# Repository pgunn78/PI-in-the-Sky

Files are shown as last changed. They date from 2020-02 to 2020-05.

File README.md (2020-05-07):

# PI-in-the-Sky
Our first semester project
## Planning
### Goals
Launch a raspberry pi into the sky measuring and recording accelerometer data along it's flight and ensure that the pi is not broken when it lands.
### Method
Using a air canon we will launch a inclosed capsule which will hold a Raspberry Pi which will be the brain of the missle, accelerometer to both measure its momentum and to know when to trigger its parachute, battery to power the Pi and Acclerometer, and parachute to slow its decent once its triggered. We can additionaly attempt to mount the air canon on somesort of mount so that it's easier to handel
### Materials
1. PVC tubing both 2 inch and 3 inch
2. Valve
3. air compressor
5. ABS plastic
6. wires
7. small lithium ion battery
8. accelerometer
9. Raspberry PI
10. 1 large parachute or multiple smaller parachutes
11. fittings
12. PVC glue/sealent
13. PVC glue Primer
14. Nuts and Bolts
15. 3mm plastic sheets
16. springs
17. PCB single sided copper material
### Timeline
#### weeks 1-2: planning and modeling
-finish projectile model
-decide on launch method
-start design of launch method
-source springs and materials
#### weeks 3-6: construction testing/Coding
-find out how to determine tilt
-build launch method
-assemble projectile
-milling of PCB
#### week 7-10: troubleshooting and polishing
-ensure that projectile stays level in flight
-work out kinks in parachute deployment
#### week 11: Launch
-launch projectile get data and assemble it into more easily understood graph
### Inital Design
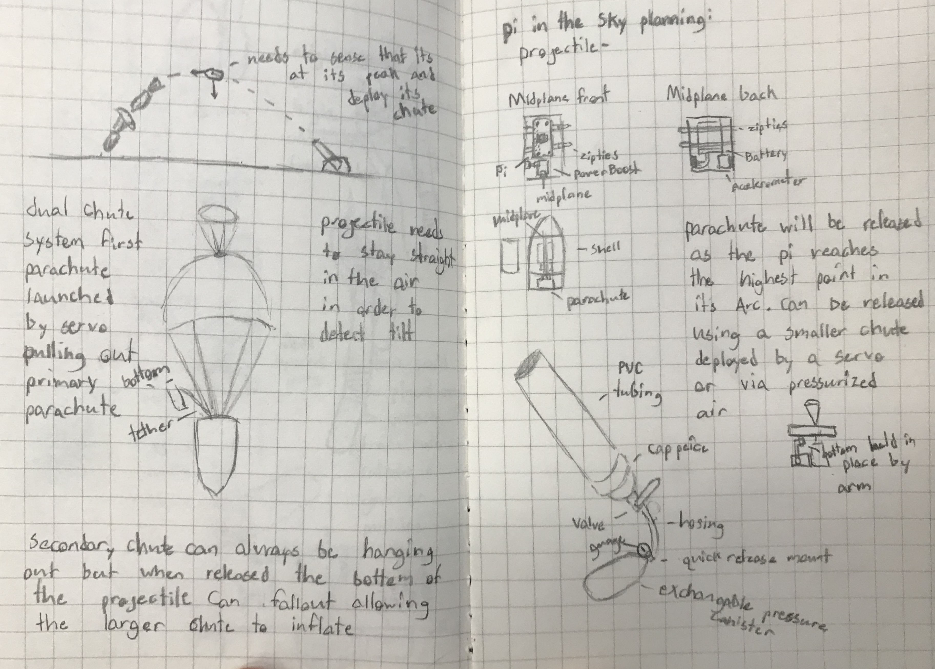
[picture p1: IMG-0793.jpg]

### Solidworks Design
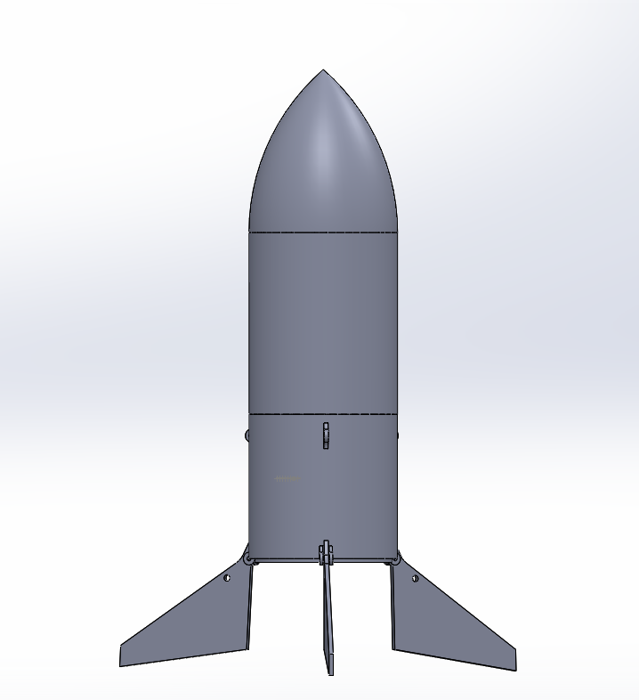
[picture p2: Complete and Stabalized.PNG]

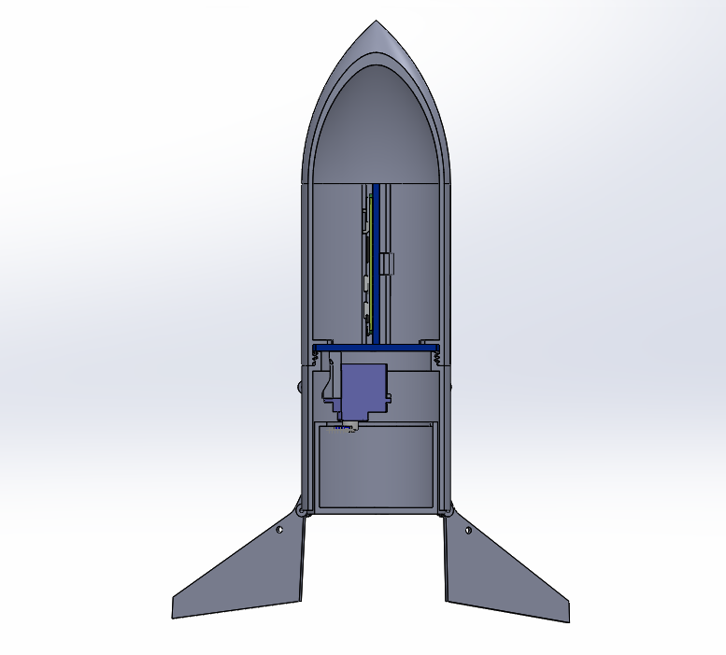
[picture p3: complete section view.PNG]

#### Design Overview
The components such as the Pi and battery are mounted on the midplane and held in place by a cap which has a hole cut in the center to run wires to a servo. Which opens to release the parachute hatch to slow down the projectile once the projectile reaches its maximum altitude. to maintain a level flight fins are mounted on the side with small extrusions to keep them held out at an ideal position.
### Code 

```

import Adafruit_LSM303
import Adafruit_GPIO.SPI as SPI
import time
import RPi.GPIO as GPIO
import pigpio
from time import sleep
#the Pi stuff below is how we get a smooth servo turn
#it just makes the pi send smother infromation waves
pi = pigpio.pi()
pi.set_mode(17, pigpio.OUTPUT)
pi.set_PWM_frequency(17,50)
sleep(1)
print(pi.get_PWM_frequency(17))

lsm303 = Adafruit_LSM303.LSM303()

while True:
    # Read the X, Y, Z axis acceleration values and print them. accel is the acceleration mag is the direction/angle
    accel, mag = lsm303.read()
    # Grab the X, Y, Z components from the reading and print them out.
    accel_x, accel_y, accel_z = accel
    mag_x, mag_y, mag_z = mag

    if 540 > mag_x > 510:
        pi.set_servo_pulsewidth(17,500)
        sleep(1)
        pi.set_servo_pulsewidth(17,2500)
        sleep(1)

    print('Mag X={0}, Mag Y={1}, Mag Z={2}'.format(
        mag_x, mag_y, mag_z))
    time.sleep(1)

```

### Wiring and PCB design
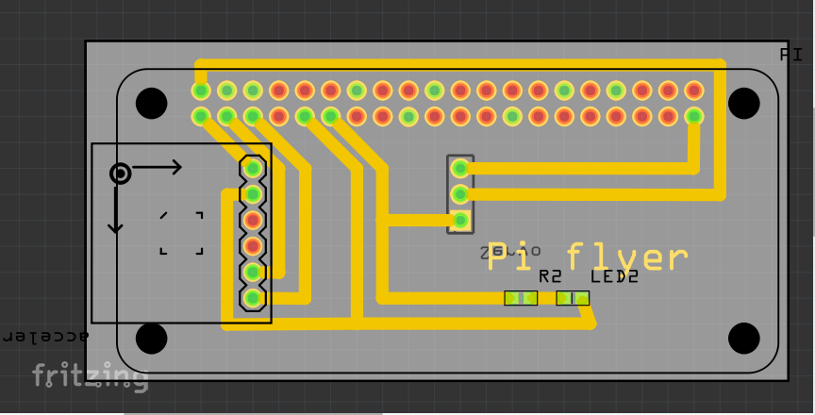
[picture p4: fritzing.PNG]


## Problems and Solutions
### SolidWorks
While doing the solidworks design the most major problem that we encountered was material use, sizeing of the projectile, and space efficiency. due to it's cylindrical shape the space inside was not the easiest to utalize properly and effectlivly while still securing the components so that they won't shift during flight. To fix this we added a midplane to secure the components onto and added another plane above that to fix the midplane during flight. In addition to providing a place to mount components this also provides ease of construction allowing us to fix all components before sliding the midplane into the projectile where there is much less space to work. by designing the projectile in a fairly bullet like shape we made it difficult for the projectile to be printed without a large amount of support material to minimize the support material needed we added a steeper slope to the shape and went into the advanced settings of the print job turning the angle down where support material was needed and allowing us to print the entire part without any material needed for the central point. The last major problem that we encountered was the sizing of certain features such as the threads which were done using the solidworks thread tool (Creating suprisingly good results). this could still present a problem as the ABC plastic is maluable enough to where a impact from the side can seperate the two pieces. Which might cause the parachute compartment to breakup when deployed spilling the internals out mid-flight, but it seems like a fairly strong connection along the length of the projectile.
### Construction of the Projectile
the largest problems in the construction of the Projectile was the header hight, PCB milling and sourcing of materials. When milling our PCB we broke the job into two different sections due to class time limitations, cutting the traces or the copper wire paths first, and then drilling the holes for the headers. this caused the holes and traces to become slightly misaligned although it did not significantly damage the board or prevent it from working. the Headers on the PCB also prevented the midplane from sliding in due to their hight to fix this we bent the header pins down in the process breaking one of the copper traces which was repaired using a section of wire which was striped of insulations and soldered on. in addition to this the LED on the board was connected to the signal pin of the servo which we fixed by breaking the connection and soldering a wire from 3V to the broken connection. The method of launching the parachute was initally a spring which with the help of a servo controlled latch would realease the parachute, both the sourcing of a spring that would meet the diminsions we needed and could store the required force was difficult prompting us to use a secondary parachute which would pull out the bottom utalizing the same servo release mechanism.

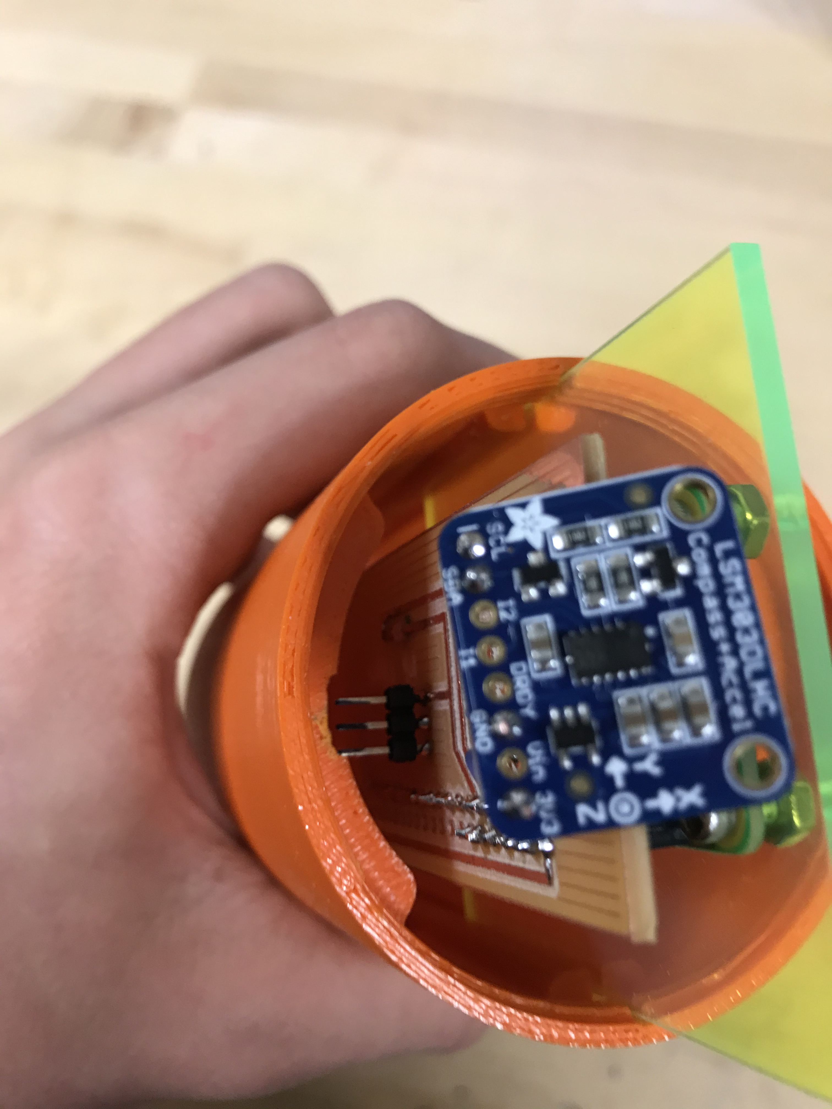
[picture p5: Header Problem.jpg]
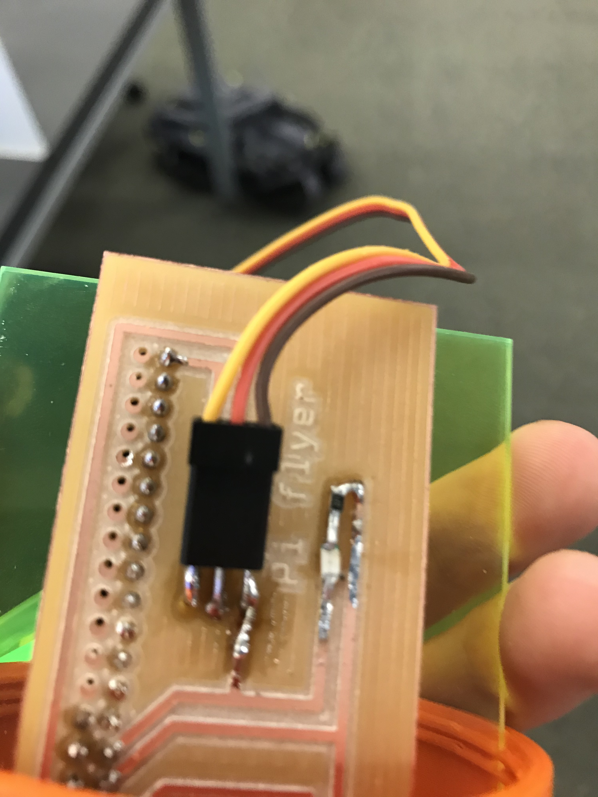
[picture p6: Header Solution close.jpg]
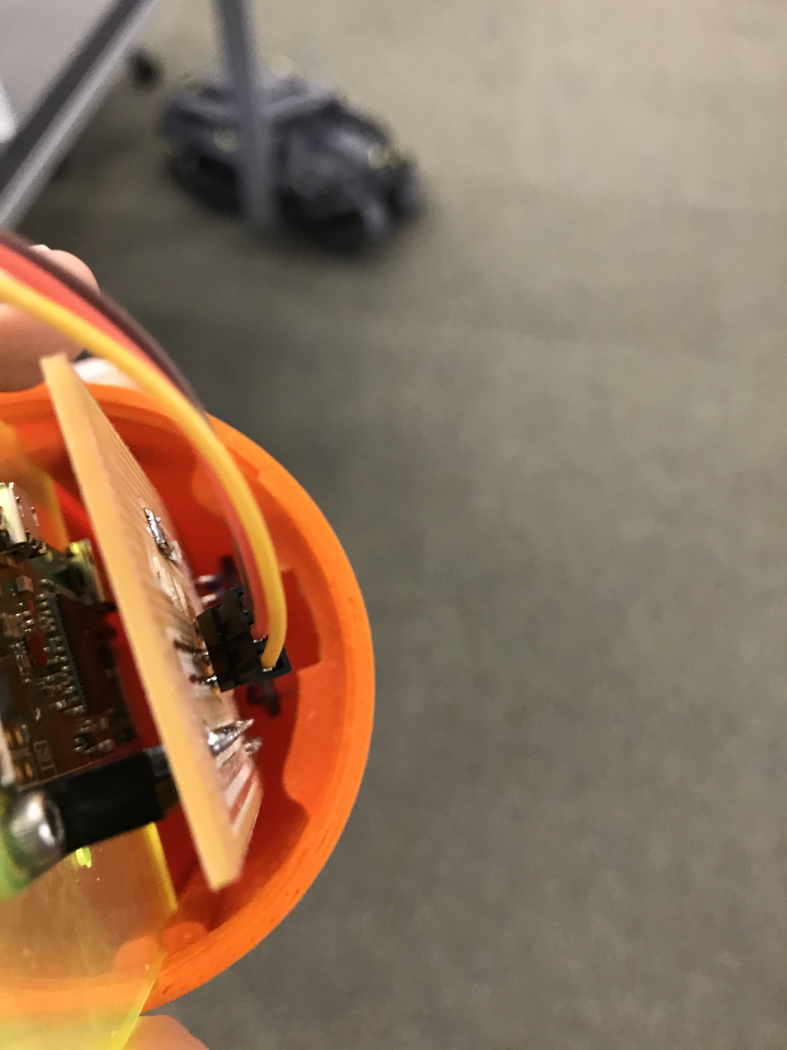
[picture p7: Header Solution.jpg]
  

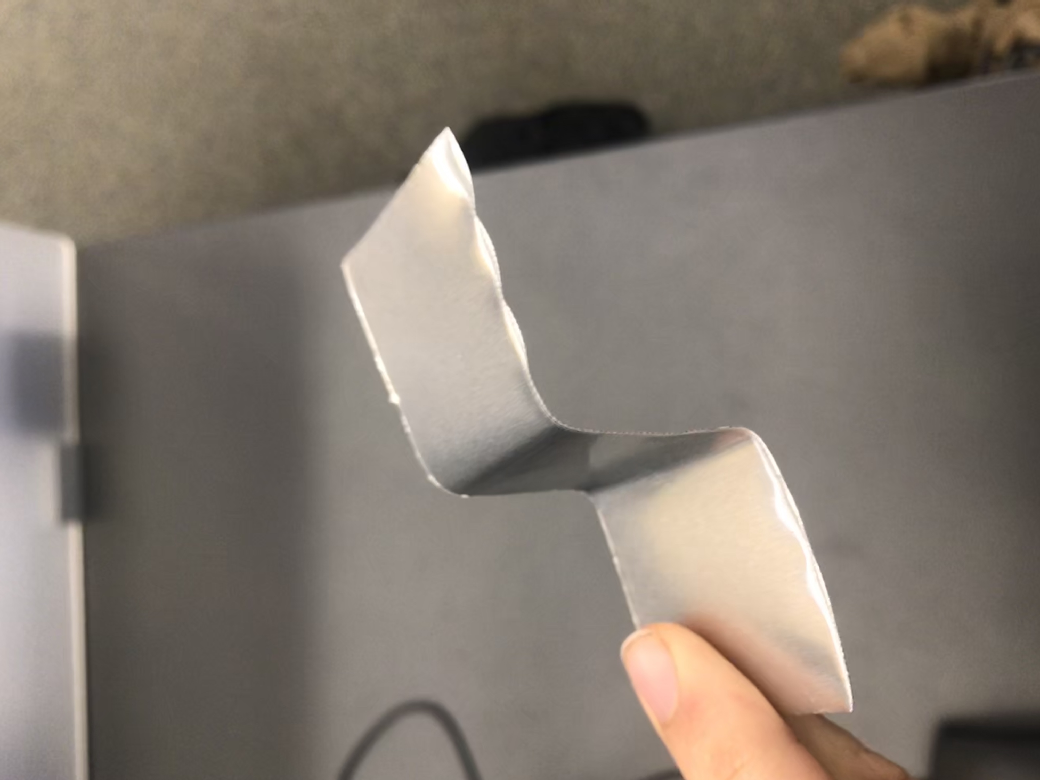
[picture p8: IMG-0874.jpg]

Attempt to create our own spring with sheet metal in the lab

### Construction of the Launcher
We had a problem with both the seals on the launcher and the size of the launch tube. the first tube we chose to use being a 3inch tube whitch served to be two narrow to fit the projectile with the fin connections points prompting us to go up a tube size requiring a four inch diameter tube presenting a additional problem where air would escape past the sides of the projectile which was fixed by placing a end cap behind the projectile catching all the air. To fix the seals on the launcher we had to both retape the fittings using a large amount of plumbers tape and switch out the schrodinger valves we were using to another company which proved to be more reliable.
### Code
We had some problmes in the beginging with twitching servos and unrleliable movment. This problem was solved when we implemented the pigpio library wich allows us to smooth out our data signals. Our code runns as soon as our pi turns on allowing us to not only capture data of the flight but also the launch getting this to happen was innitally a problem due to the fact taht multiple words in the command were misspeld. Most importantly we have our code set up to record all of our data into a file called flightlog.
## Test 1
For the First test we dropped the projectile from the 2nd floor down to the first floor cushioning the impact, and testing the fins ability to stabalize flight. Several weak points arose the first of which being the thickness of the fin supports, which broke on impact, and the second being the mating between the threads which proved to weak to hold the projectile together and had to be secured using tape.

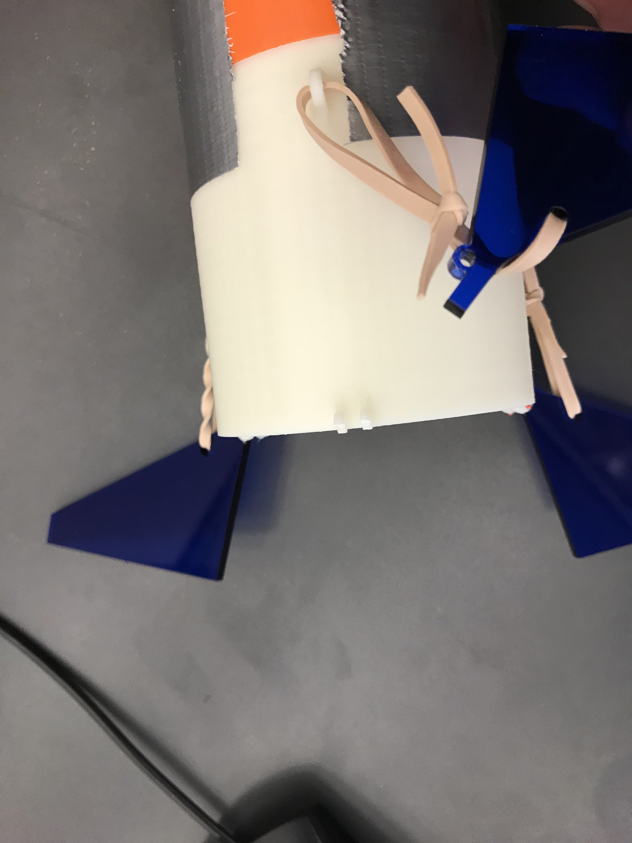
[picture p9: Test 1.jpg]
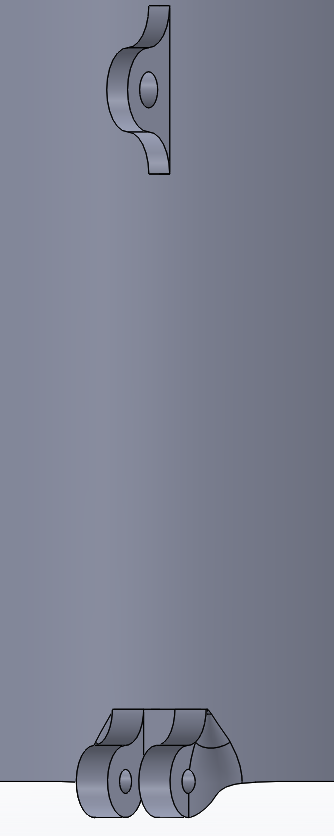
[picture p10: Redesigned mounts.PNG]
 

### Solution
to fix this we thickened the supports and added fillets to them within the solidworks design to both arrest movement horizontaly and verticaly. Additionally we widened the holes where the rubberbands were secured for ease of construction in the future. To fix the threading issues we lowered the Tolerance between the threads but printing larger threads or more would have required a reprint of the main capsule.

## Test 2
In the second test we dropped the projectile from the roof with the parachute attached this allowed us to test how well the parachute was able to slow down the projectile and whether or not the drag from wind alone would be able to deploy the parachute. it proved to be mostly successful the main problem being the impact once it reached the ground snapping the deployable wings which was expected although it snapped in a unusal place just below the attachment point.

#### Video link

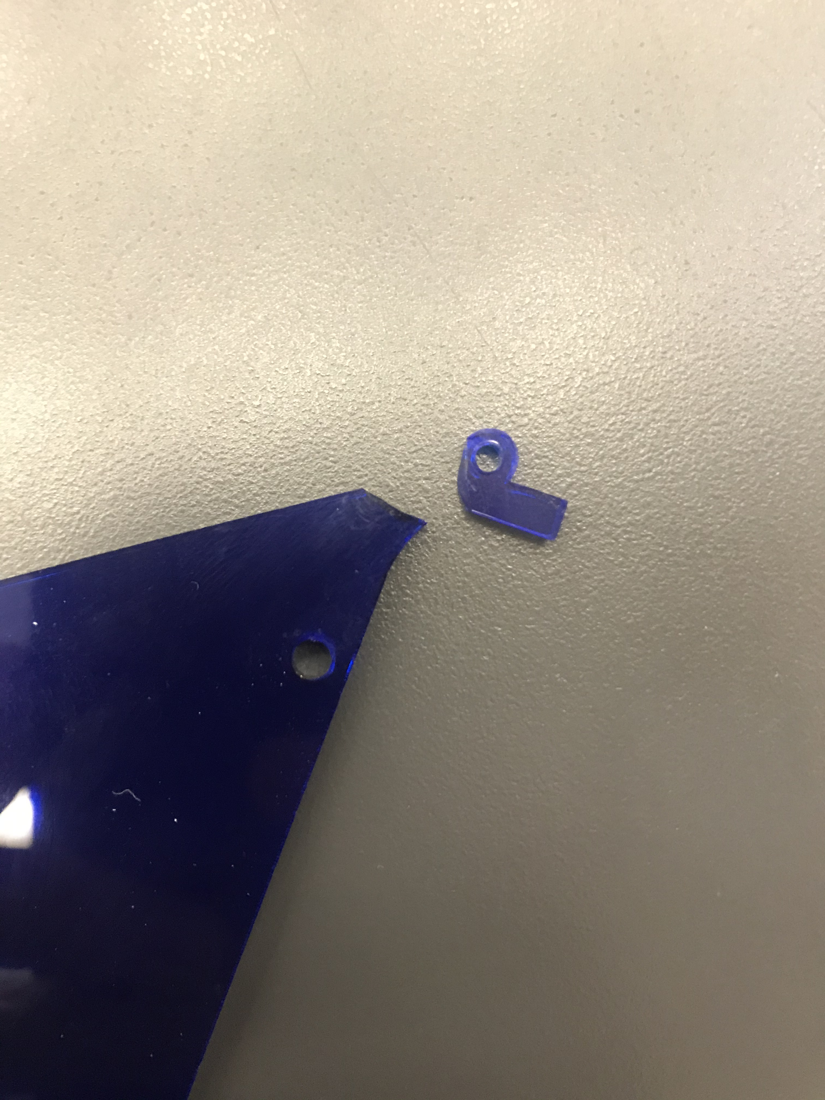
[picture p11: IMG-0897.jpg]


### Solution
we didn't change anything about the fins as we have additional parts to replace them with one possible solution in the future being to cut or mill them from a stronger/thicker material.

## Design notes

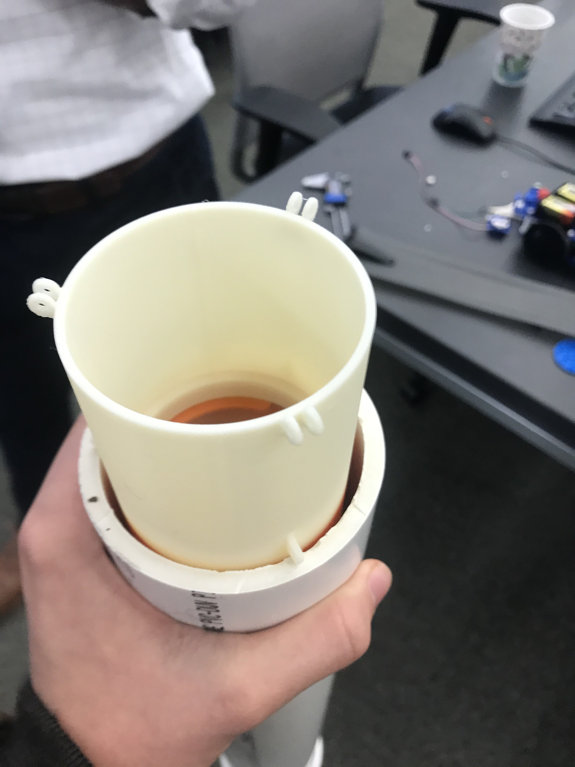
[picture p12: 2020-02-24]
switch to 4in.jpg

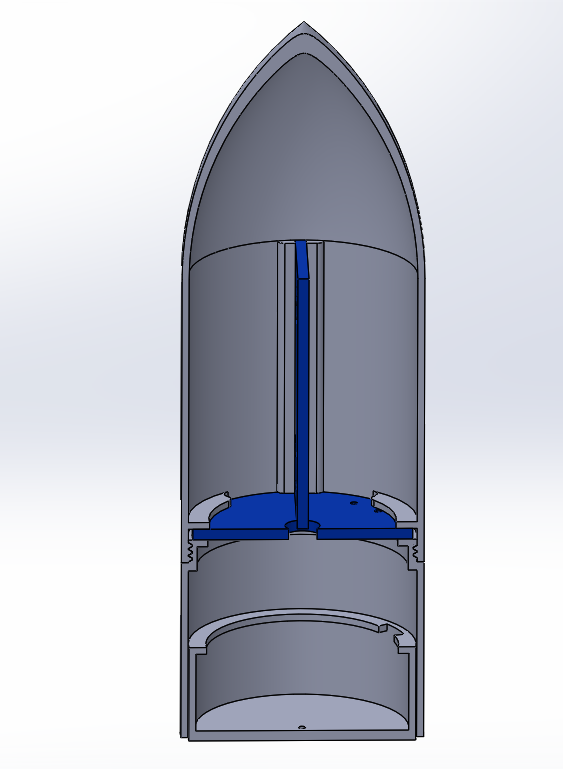
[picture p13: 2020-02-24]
Casing.PNG

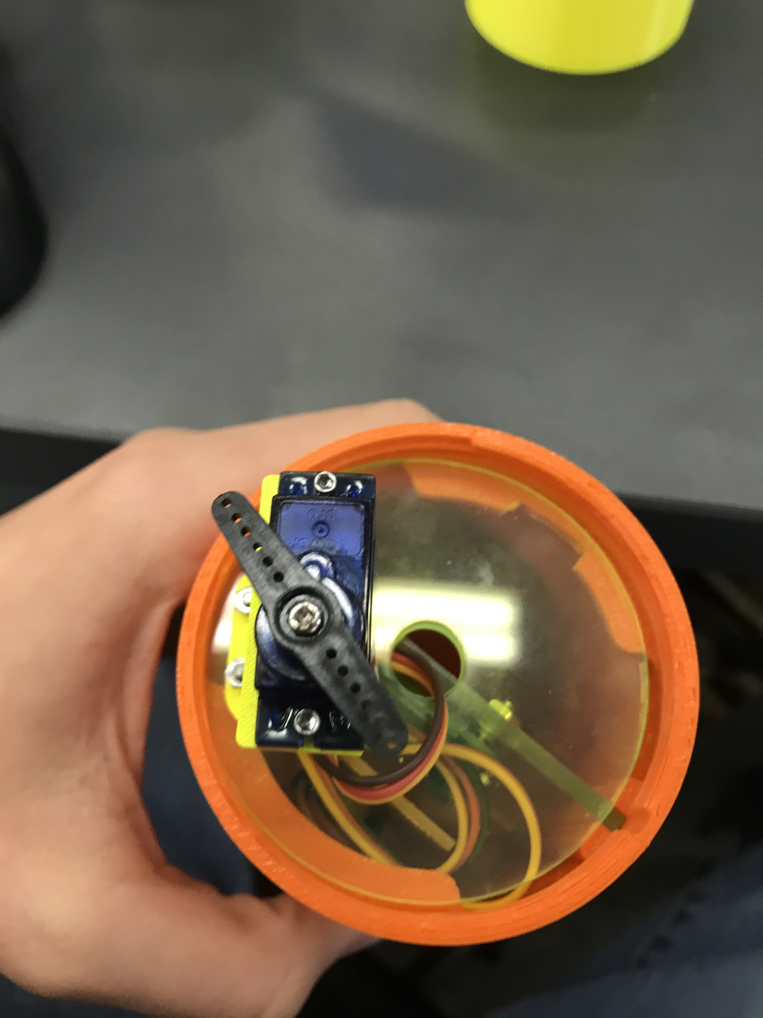
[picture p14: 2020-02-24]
Midplane fitting.jpg

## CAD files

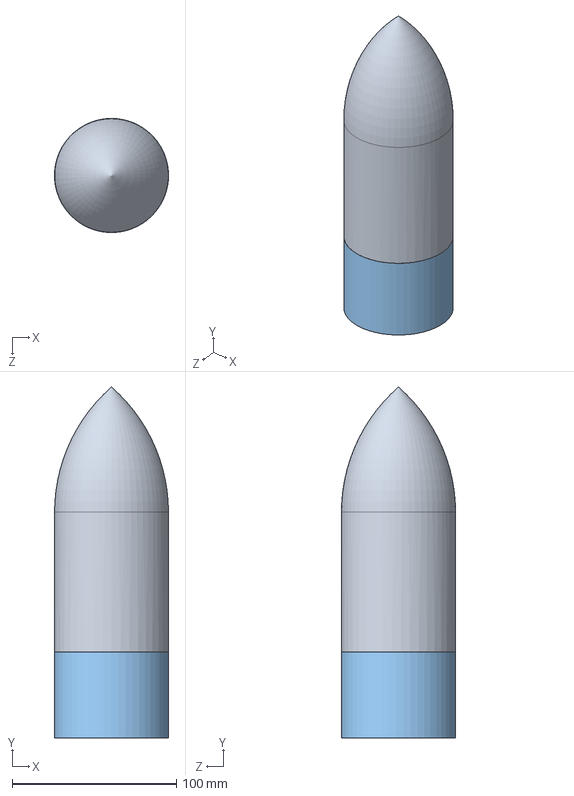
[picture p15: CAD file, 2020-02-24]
Projectile assembly.SLDASM
69.5 x 213.7 x 69.5 mm
projectile
compartment cap
chute compartment
Midplane
RaspberryPiZeroW
Battery
Micro Servo SG92R 180
Bottom
servo holder
Micro Servo Horn Single Arm

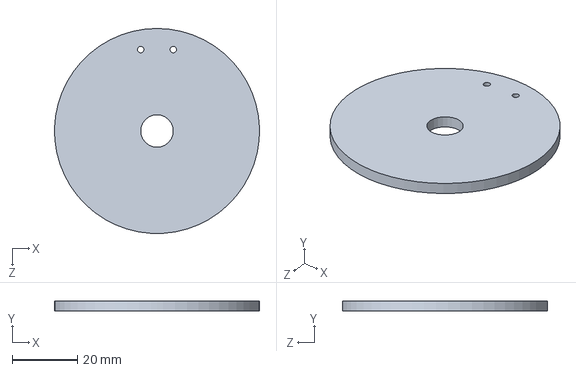
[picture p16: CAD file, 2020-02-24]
compartment cap.SLDPRT
63.0 x 3.18 x 63.0 mm

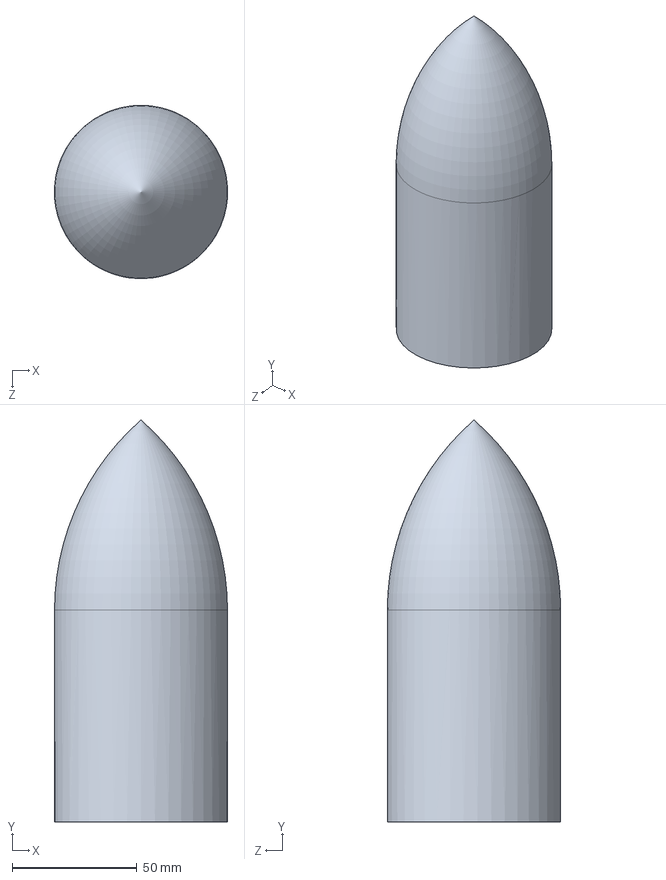
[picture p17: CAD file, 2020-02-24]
projectile.SLDPRT
69.4 x 161.2 x 69.5 mm

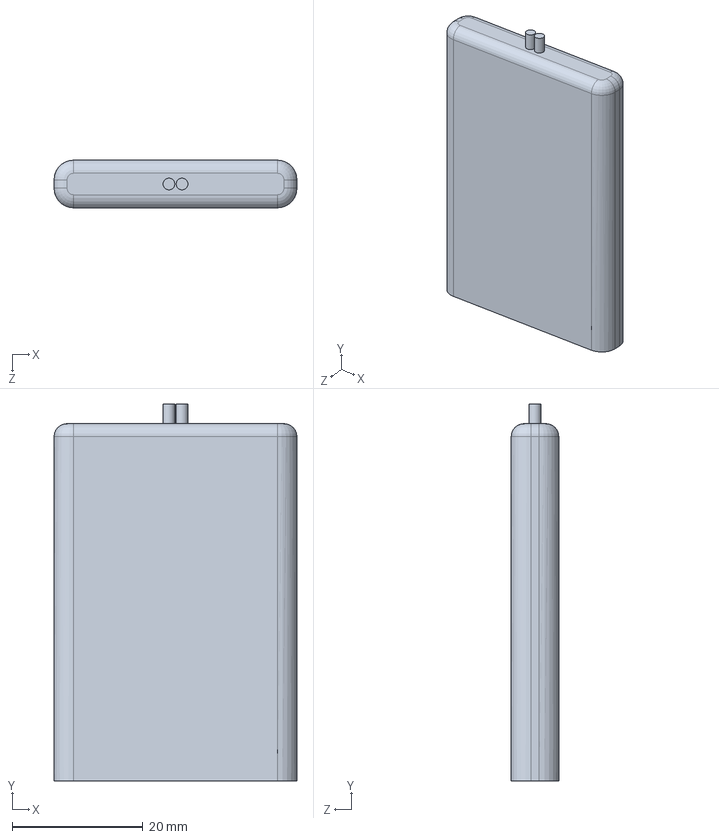
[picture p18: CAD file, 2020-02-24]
Battery.SLDPRT
37.2 x 57.7 x 7.30 mm

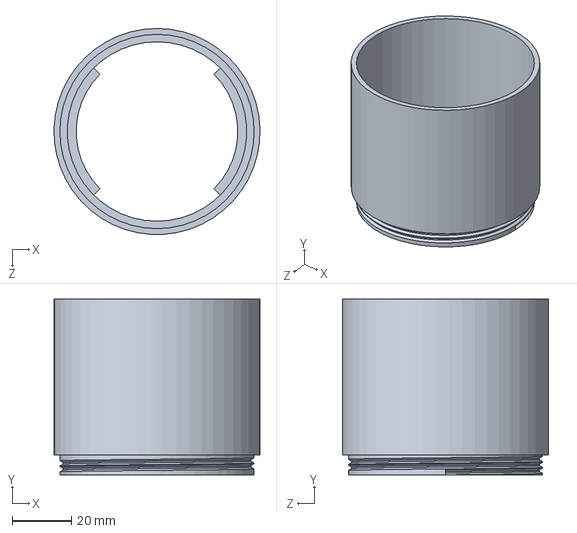
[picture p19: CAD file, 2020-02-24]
chute compartment.SLDPRT
69.5 x 59.2 x 69.5 mm

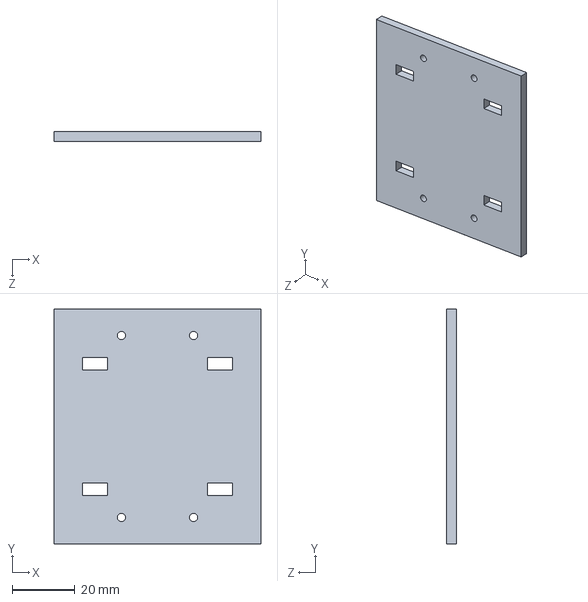
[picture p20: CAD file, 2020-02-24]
Midplane.SLDPRT
66.0 x 75.0 x 3.18 mm

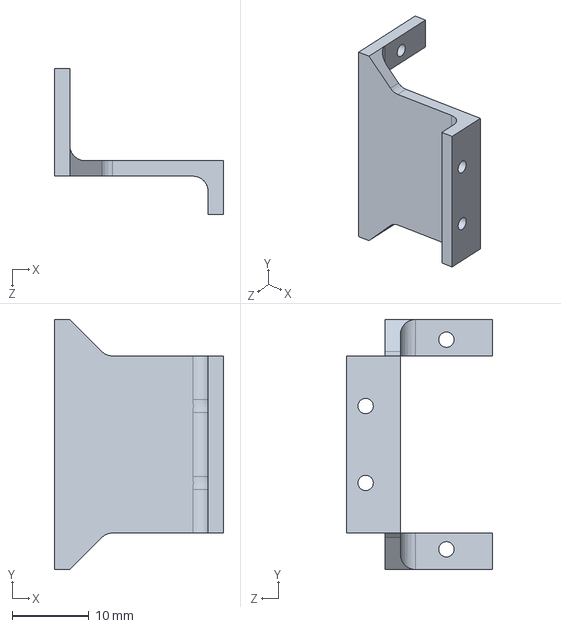
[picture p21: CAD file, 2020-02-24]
servo holder.SLDPRT
22.0 x 32.5 x 19.0 mm

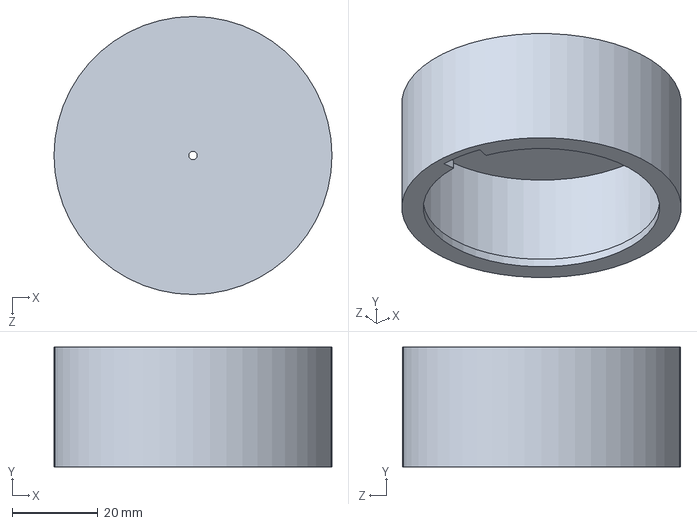
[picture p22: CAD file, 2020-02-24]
Bottom.SLDPRT
65.0 x 28.0 x 65.0 mm

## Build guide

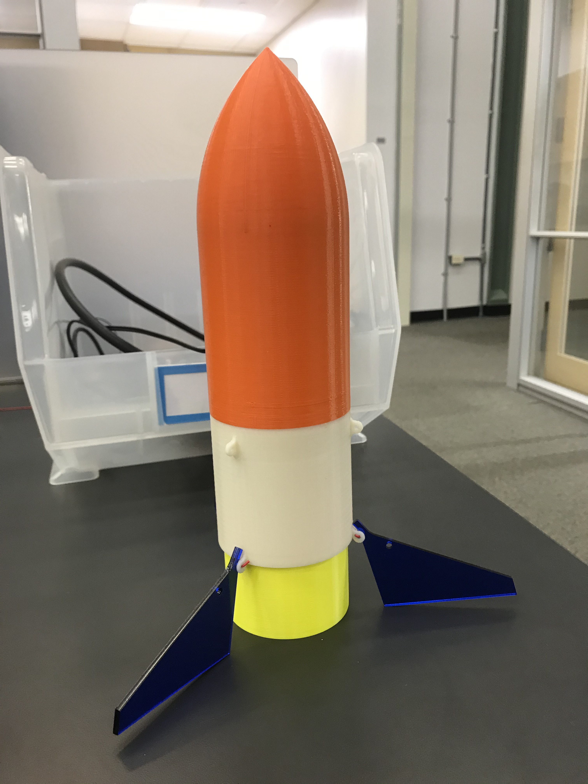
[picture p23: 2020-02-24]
complete 3d printed.jpg

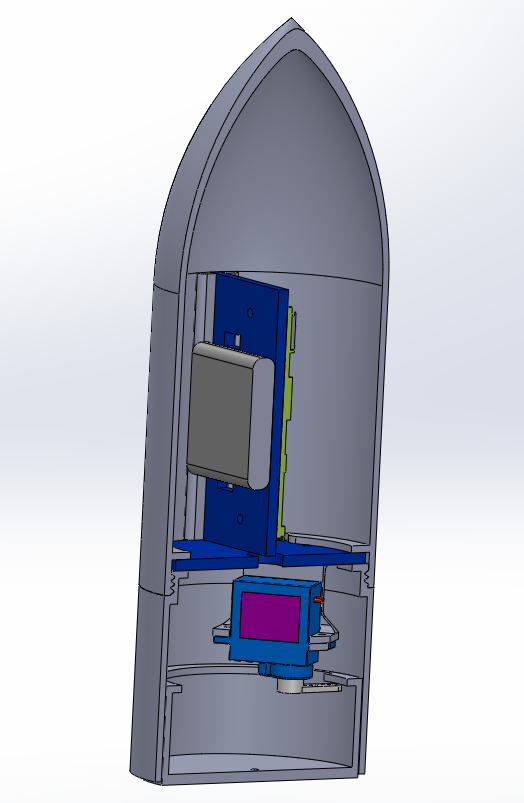
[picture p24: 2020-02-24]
Finished Assembly.PNG

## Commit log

2019-12-03 Uploading projectile SW part, no git folder found?
    Zane, where is the git folder?
    [projectile.SLDPRT]
2020-03-13 self calibrate + better deployment
